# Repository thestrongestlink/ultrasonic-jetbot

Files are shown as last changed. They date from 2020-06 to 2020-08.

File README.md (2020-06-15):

# Add an Ultrasonic Sensor to your Jetbot

The Nvidia Jetbot offers an excellent opportunity to explore the Nvidia Jetson Nano, do some nice 3D printing and learn AI at the same time. This Git contains all information for adding a ultrasonic sensor to your Jetbot. 

ultrasonic-jetbot

This repository contains:

* The 3D-printable file in the cad-files folder (in STL format), 
* Sample source code in Python for the Jetbot in the source folder, 
* Sample source code in C for the M0 microcontroller, 
* A bill of materials, and a short assembly instructions for the modification of the Nvidia Jetbot in the doc folder.

A complete write-up of the modification can be found on my [blog](https://thestrongestlink.nl/2020/05/31/ultrasonic-sensor-for-the-jetbot/).

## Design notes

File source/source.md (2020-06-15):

# Source Files

Source files in this folder:

* ultrasonic_ic.c : C-code for Adafruit Feather M0 Micro controller interfacing ultrasonic sensor with I2C
* ultrasonic_drive.py: Python-code for Jetson Nano navigating Jetbot around the room using ultrasonic sensor.

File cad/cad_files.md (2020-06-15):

# Cad Files

Cad files can be found in this folder.

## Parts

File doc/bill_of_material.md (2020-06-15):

# Bill of Material

For this project you will need following:

* 1 complete and functioning Jetbot,
* 1 3D printed front, 
* 1 Adafruit Feather M0 microcontroller,
* 1 set of short female headers for the Adafruit Feather,
* 1 set of male headers for the Adafruit Feather,
* 2 of 10K resistors,
* 4 of microscrews to fix the sensor and the 3D printed front,
* Some multicolored (jumper) wires.

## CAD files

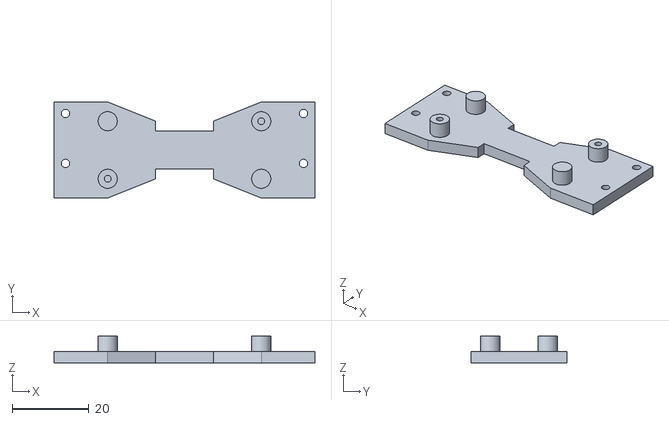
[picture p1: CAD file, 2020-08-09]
cad/UltrasoonFronJetBot_40mm v3.stl
68.0 x 25.0 x 7.00

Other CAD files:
cad/UltrasoonFronJetBot_v10.stl

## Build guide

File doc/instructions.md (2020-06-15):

# Instructions

1. Print the plastic front for holding the ultrasonic sensor on a 3D printer.
2. Solder on the short female headers to the Feather M0. The female headers should be soldered facing upwards (i.e. the headers and components are on the same side). 
3. Wire up the ultrasonic sensor to the Feather and run a test to check proper function of the sensor and the feather. 

Note that the SRF05 sensor requires 5V power and the Feather runs on 3.3V. While the Trig signal can be 3V or 5V, the ‘return’ Echo signal is 5V logic. As the Feather can only handle 3.3V, use the two resistors as a divider to convert the 5V logic level to a safe 2.5V. Be careful with wiring up to prevent damage to the Feather.

4. Connect the SRF05 GND to a GND pin of the Feather M0,
5. Connect the second GND pin of the Feather M0 to a Jetson Nano GND pin,
6. Connect the SRF05 VCC to the 5V power pin of the Jetson Nano,
7. Connect the SRF04 TRIG pin to pin 11 of the Feather M0,
8. Connect the SRF04 ECHO via a divider bridge (using the two resistors) to pin 12 of the Feather M0.

If done correctly, your test assembly should resemble something like the breadboard lay-out as shown.

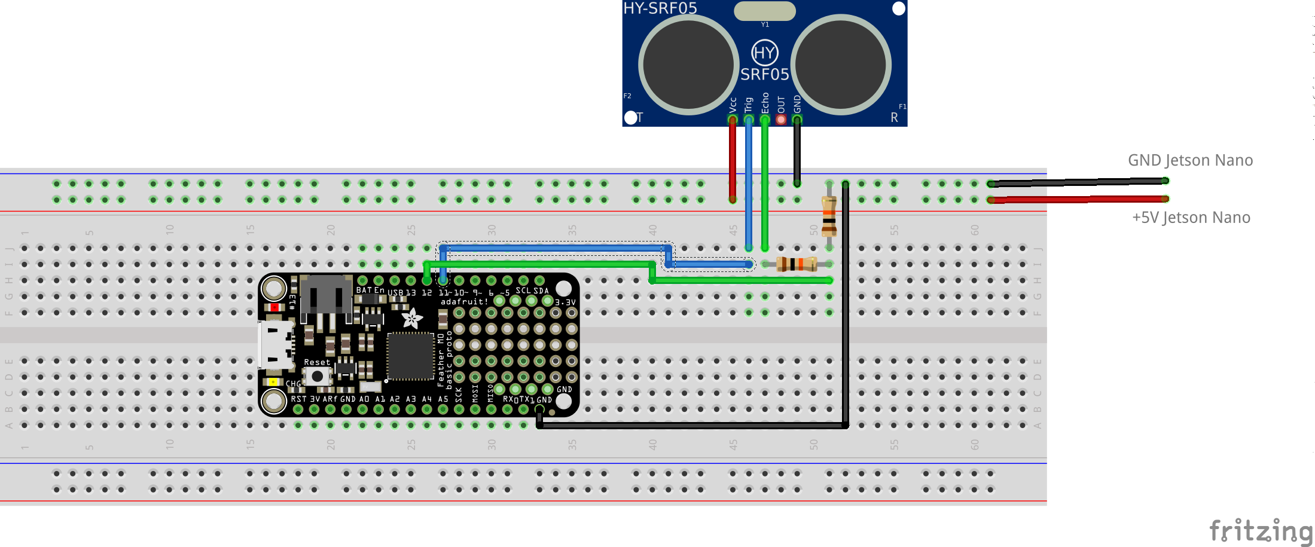
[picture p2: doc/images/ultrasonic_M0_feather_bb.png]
breadboard


9. Start up the Jetson Nano so that 5V is provided to the sensor, hook up a USB cable between the feather and your computer and upload the source code ultrasonic_ic.c using the Arduino IDE.
10. When uploading is completed, open the Arduino Monitor. Hold your hand in front of the sensor and the distance between the sensor and your hand should be displayed in the monitor. Move your hand closer and further away from the ultrasonic sensor and note the changing readout on the monitor. 
11. Switch off power on both Jetson Nano and the Feather M0. 
12. Temporarily disconnect the I2C connection to the motor driver from pins 3 and 5 of the Jetson Nano (remember their positions!).
13. Make an I2C connection between the Jetson Nano and the Feather M0. You do this by connecting the SCL pin of the Feather M0 with the SCL pin of the Jetson Nano (pin 5) and connecting the SDA pin of the Feather M0 with the SDA pin of the Jetson Nano (pin 3). 
14. Power up again and once the Jetbot software has loaded, connect to the JupyterLab interface on your computer and create a new python session. 
15. Upload the short Python test script ultrasonic_test.py to JupyterLab.
16. Start the script by pressing shift-enter in JupyterLab and you should see the result of a distance measurement every second. Try holding and moving your hand at several distances from the ultrasonic sensor and note that the reported distance changes in the JupyterLab output. 

If everything works as described, you now have a working distance measurement system communicating with the Jetbot over I2C.

17. Unscrew the DC motor driver Feather Wing from the Jetbot and disconnect the jumper wires from the Feather M0 microcontroller. 
18. Desolder the 2-pin and 3-pin headers on the motor driver, move these headers to the inner rows of the DC motor driver board same pins and resolder. 
19. Solder an additional 2-pin header to pins 11 and 12 of the DC motor driver board using the inner rows, and solder a 1-pin header to the second GND of the DC motor driver board. 
20. Solder the new short male headers strips to the bottom of the DC motor driver board. 
21. Position the M0 Feather on the location of the motor driver and secure in place using the micro screws that where used to hold the motor driver in postion.
22. Fasten the ultrasonic sensor to the 3D printed front using two micro screws. 
23. Connect the jumper wires to the sensor if required and then fasten the 3D printed front to the Jetbot using two micro screws in the top holes of the 3D printed front.
24. Fix the motor driver Feather Wing in place on top of the M0 Feather by inserting the short male headers into the short female headers and re-attach the jumper wires in their original positions. 
25. Connect the ECHO and TRIG pins of the ultrasonic sensor to the 2-pin header (pins 11 and 12) of the motor driver Feather Wing.
26. Connect the GND pin of the ultrasonic sensor to the second GND single header pin on the motor driver. 
27. Route the 5V jumper wire from the sensor to the 5V pin of the Jetson Nano. Reconnect the I2C wires you disconnected from the Jetson Nano earlier. 
28. Check all your wiring one last time and power up the Jetbot, open the JupyterLab environment on your computer and try the ultrasonic_drive.py Python Script to prove the integration has been succesful.

If all’s well, your Jetbot should now be cruising along the floor and once it encounters a wall it will back up a little bit, make a left turn and will then continue it’s journey. More information can be found at https://thestrongestlink.nl.

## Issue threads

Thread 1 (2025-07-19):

Dead link to blog and missing image(s)

greenonline, 2025-07-19:
I am so glad that I found this Github repo. I originally read your blog when it was first published, and got most of the parts. Then the page (site?) vanished, and I have been floundering around looking for scraps of info (from waybackmachine and google caches), which I took the liberty of (partially) reproducing on, [Archive: Ultrasonic Sensor for the Jetbot](https://gr33nonline.wordpress.com/2023/02/15/archive-ultrasonic-sensor-for-the-jetbot/).

However, the third image (in your blog), of the underside of the jetbot (Previously titled *(11 June 2020): Motor Driver Feather Wing piggy-backed on M0 Feather and all jumper cables attached*), I have not been able to locate and it is missing from this Git repo. Could you add it to this repo?

Plus the links to your blog don't work any longer, so maybe they should be removed... or, better still, re-upload the original blog site into a directory in this repo, as it really was rather good (I had read a fair few pages before it got taken down).

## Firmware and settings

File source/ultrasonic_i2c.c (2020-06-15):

/*
Ultrasonic sensor for Jetbot
----------------------------
Trigger on port 11
Respons on port 12
5V to 3.3V response conversion with 2.2K and 4.7K resistors
I2C slave sender on port 8
----------------------------
This sketch is based on the Ping))) Sensor sketch created by David A. Mellis on 3 Nov 2008, modified by Tom Igoe on 30 Aug 2011 and modified by Ron in 2020 to 
include I2C communications.
----------------------------
The original source of Ping))) can be found on:
  http://www.arduino.cc/en/Tutorial/Ping
This example code is in the public domain.
*/

#include <Wire.h>

// this constant won't change. 
// It's the pin number of the sensor's output:
const int pingPin = 11;
const int distPin = 12;
long cm;

void setup() {
  // initialize serial communication:
  Serial.begin(9600);
  pinMode(pingPin, OUTPUT);
  pinMode(distPin, INPUT);
  Wire.begin(8);
  Wire.onRequest(requestEvent);
}

void loop() {
  // establish variables for duration of the ping, 
  // and the distance result in inches and centimeters:
  long duration, inches;
  // The PING))) is triggered by a HIGH pulse of 2 
  // or more microseconds.
  // Give a short LOW pulse beforehand to ensure a clean 
  // HIGH pulse:
  digitalWrite(pingPin, LOW);
  delayMicroseconds(2);
  digitalWrite(pingPin, HIGH);
  delayMicroseconds(5);
  digitalWrite(pingPin, LOW);
  // A HIGH pulse whose duration is the time (in 
  // microseconds) from the sending of the ping
  // to the reception of its echo off of an object.
  duration = pulseIn(distPin, HIGH);
  // convert the time into a distance
  // inches = microsecondsToInches(duration);
  cm = microsecondsToCentimeters(duration);
  // Print distance to serial monitor for testing
  Serial.print(cm);
  Serial.print("cm");
  Serial.println();
  delay(100);
}

// I2C function that executes whenever data is requested 
// by master. This function is registered as an event, 
// see setup()
void requestEvent() {
  byte buf[4];
  buf[0] = (byte) cm;
  buf[1] = (byte) cm>>8;
  buf[2] = (byte) cm>>16;
  buf[3] = (byte) cm>>24;
  Wire.write(buf, 4); // respond with message of 4 bytes 
                      // (cm is long type)
  Serial.println("I2C request");
}

long microsecondsToInches(long microseconds) {
  // According to Parallax's datasheet for the PING))), 
  // there are 73.746
  // microseconds per inch (i.e. sound travels at 1130 
  // feet per second).
  // This gives the distance travelled by the ping, 
  // outbound and return,
  // so we divide by 2 to get the distance of the 
  // obstacle.
  // See: http://www.parallax.com/dl/docs/prod/acc/28015-PING-v1.3.pdf
  return microseconds / 74 / 2;
}

long microsecondsToCentimeters(long microseconds) {
  // The speed of sound is 340 m/s or 29 microseconds 
  // per centimeter.
  // The ping travels out and back, so to find the 
  // distance of the object we take half of the distance 
  // travelled.
  return microseconds / 29 / 2;
}
When uploading is completed, open the Arduino Monitor. Hold your hand in front of the sensor and the distance between the sensor and your hand should be displayed in the monitor. Move your hand closer and further away from the ultrasonic sensor and note the changing readout on the monitor. Once you have this functioning, we’re ready for the next step; interfacing with the Jetson Nano using I2C.

Switch off power on both Jetson Nano and the Feather M0. Now temporarily disconnect the I2C connection to the motor driver from pins 3 and 5 of the Jetson Nano (remember their positions!) and make an I2C connection between the Jetson Nano and the Feather M0. You do this by connecting the SCL pin of the Feather M0 with the SCL pin of the Jetson Nano (pin 5) and connecting the SDA pin of the Feather M0 with the SDA pin of the Jetson Nano (pin 3). Now power up again and once the Jetbot software has loaded, connect to the JupyterLab interface on your computer and create a new python session. Copy and paste the following short Python test script to JupyterLab:

import smbus
import time

bus = smbus.SMBus(1)
address = 8 # I2C address for Ultrasonic bus

def distance():
    """Returns distance measured by ultrasonics in cm"""
    return bus.read_byte_data(address, 0)

while True:
    print(distance(), " cm")
    time.sleep(1.0)

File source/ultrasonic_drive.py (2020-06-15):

from jetbot import Robot
import smbus
import time

robot = Robot()
bus = smbus.SMBus(1)
address = 8 # I2C address for Ultrasonic bus

def distance():
    """Returns distance measured by ultrasonics in cm"""
    return bus.read_byte_data(address, 0)

while True:
    if (distance() < 20):
       robot.backward(0.4)
       time.sleep(0.6)
       robot.left(0.4)
       time.sleep(0.5)
    else:
       robot.forward(0.4)

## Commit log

2020-06-15 Create bill of material
2020-08-09 Add files via upload
    9/8/20: Please note that the initial design is for an ultrasonic sensor with mounting holes positioned at 15 mm x 38.1 mm, However, I was kindly informed that there are also ultrasonic sensors with m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
    [UltrasoonFronJetBot_40mm v3.stl]
